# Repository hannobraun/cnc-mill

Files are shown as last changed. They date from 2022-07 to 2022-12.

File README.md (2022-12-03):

# CNC Mill

## Goal

I'd like to have a 3-axis CNC mill. I've considered buying one, but everything I can find violates one or more of the following constraints:

- **Budget:** It's going to be my first CNC mill, so spending a lot of money doesn't make much sense. The main purpose is to learn, and figure out what I actually need in a CNC mill. For that reason, I'd like to keep the budget below 1000€.
- **Capability:** At the same time, I don't want to buy a machine that I will outgrow within the first week. It should be capable of cutting aluminium.
- **Space:** I'm severely limited on space. It needs to comfortably fit on a desk.
- **Environment:** I don't have a proper workshop, unfortunately. The machine will need to run in my apartment, preferably without disturbing the neighbors.

There simply doesn't seem to be a machine like this, which is not a surprise. For this reason, I'd like to try and build my own, purpose-made for my use case.

I suspect it might simply be impossible to fulfill all of these requirements within the limited budget. If that is the case, I'm looking forward to learning what the limitations are specifically. I'm also aware that there's a high risk that a self-built machine will fall short in some or all of these areas. I think it's still likely to be a good investment, for the learning experience alone.

## Status

This project has stalled while in the planning phase. I was at the point where the calculations I wanted to do were way beyond my knowledge, so I had to do quite a bit of studying to make progress. Then my daily schedule shifted from under me and I was left with very little time to continue doing that.

I'm sure at some point, I'll have both the desire and the time to design my own CNC mill again. Whether I'll pick back up here when that time comes, or if I decide to start fresh, I don't know.

## License

This project is open source. All documents, design files, and software in this repository are available under the terms of the [Zero Clause BSD License] (0BSD, for short). This basically means you can do anything with them, without any restrictions, but you can't hold the authors liable for problems.

See [LICENSE.md] for full details.

[Zero Clause BSD License]: https://opensource.org/licenses/0BSD
[LICENSE.md]: LICENSE.md

## Design Decisions

Here are some high-level design decisions I've made. None of them are final, and they might still change as I do more research:

- **Configuration:** Fixed gantry. The advantages are just too big, and I think I can live with a smaller work area in one axis.
- **Size:** 40x40x40 cm³ or thereabouts. Those are outer dimensions. If it turns out that this leaves not enough working area, I can go a bit larger, especially in height.
- **Spindle:** 1.5 kW air-cooled AC spindle. Should be strong enough to do well in aluminium and avoids the additional complexity of water-cooling.
- **Axis motors:** Stepper motors. I haven't really looked into servos, but seeing how many machines run just fine with steppers, I'm pretty confident they will work for me. An open-loop control system will also reduce cost and complexity.

## Parts

- eBay
  - [Zhong Hua Jiang 1.5 kW Air-Cooled CNC Spindle Motor 80mm](https://www.zhonghuajiangspindle.com/1.5kw-cnc-air-cooled-spindle-motor-80mm.html): Those are widely available on eBay. Preferably ER16, but ER11 is acceptable.
  - 1.5 kW Huanjang VFD: there are sets of those and the aforementioned spindle available
- Sorotec
  - [Spindle Clamp](https://www.sorotec.de/shop/Spindelhalter-f-r-80mm-HFS-Spindeln-4085.html): Lots of the spindle/VFD sets on eBay come with a clamp, but those don't have mounting holes. This one looks nicer.

## Research Notes

These are the notes from my research process.

### Other Machines

It's going to make sense to take inspiration from other machines at some point. Here are some links:

- [**OpenBuilds**](https://openbuilds.com/): Lots of machines of all kinds.
- [**MPCNC**](https://docs.v1engineering.com/mpcnc/intro/): Interesting design. Less traditional than what I have in mind.
- [**Tormach xsTECH**](https://tormach.com/machines/routers/xstech-router.html): Really interesting machine, in terms of configuration, form factor, and enclosure. Pretty much what I want to build, but hopefully I can fit some more rigid components into the budget.
- [**PrintNC**](https://wiki.printnc.info/en/home): Moving gantry design with a frame based on steel tubing.
- [**Millennium Mill**](https://www.reddit.com/r/MilleniumMachines/): C-frame mill based on aluminium extrusion.
- [**ULTIMATE Bee**](https://bulkman3d.com/knowledge-base/ultimate-bee/): Classic moving gantry design, with what looks like high-quality components.
- [**PocketNC**](https://pocketnc.com/): 5-axis desktop CNC mill. Interesting, in that it is used for milling aluminium (easy to find examples on YouTube), but has a relatively weak spindle (200W).
- [**Nomad**](https://carbide3d.com/nomad/): Pretty close to what I would like to build, in regards to the configuration, form factor, and enclosure. Notable for its weak spindle (70W).

### Online Shops

I'm looking into two groups of online shops:

- Local (i.e. European) shops, because that gives me a minimum of hassle (shipping, customs).
- Shops on platforms like AliExpress or eBay with low prices, as that might be necessary to meet my budget.

European shops:

- [**cnc-technics:**](https://shop.cnc-technics.de/): Have lots of relevant products, but probably too high-end for my budget.
- [**DOLD Mechatronik**](https://dold-mechatronik.de/): Have a lot of different stuff, including aluminium in various sizes. At least some categories seems to be high-priced, relative to the available budget.
- [**Sorotec**](https://www.sorotec.de/shop/): Large selection of all kinds of stuff required for CNCs.
- [**MISUMI**](https://de.misumi-ec.com/): Large selection of materials, mechanical components, and much more. Lots of options for modifying material and aluminium extrusion parts.
- [**Motedis**](https://www.motedis.com/): Materials and mechanical components.

AliExpress:

- [**Bulk Man 3D**](https://www.aliexpress.com/store/1752067) ([also have a website](https://bulkman3d.com/)): Large selection of lots of things I'm going to need.
- [**Makerbase**](https://www.aliexpress.com/store/1047297): Control boards mostly seem not applicable, but the stepper drivers are very interesting.
- [**Zhong Hua Jiang**](https://de.aliexpress.com/store/214974): They manufacture spindles that they sell there, as well as other useful things.

eBay:

- [**motor-mall**](https://www.ebay.de/str/motormall): Chinese shop, ships from Europe. Has spindles and VFDs.
- Those seems to be essentially the same:
  - [**kuku081**](https://www.ebay.de/str/kuku081)
  - [**kuku281**](https://www.ebay.de/str/kuku218)
  - [**kuku86**](https://www.ebay.de/str/kuku86)
  - [**powave21**](https://www.ebay.de/str/powace21)
  - [**rattmmotor**](https://www.ebay.de/str/rattmmotor)
  - [**rattmmotor88**](https://www.ebay.de/str/rattmmotor88)
  - [**RATTM MOTOR CNC**](https://www.ebay.de/str/rattmmotorcnc)
- [**chinacnczone-de**](https://www.ebay.de/str/cnczonedd)

### Configuration

I believe that the following machine configurations are the strongest contenders:

- **Moving gantry**: Tool moves in all 3 axes.
- **Fixed gantry**: Tool moves in x and z axes, table moves in y axis.

I have ruled out more exotic configurations for my first build (despite having lots of ideas), to reduce overall risk.

References:

- https://cncchronicle.com/fixed_or_moving_gantry_for_cnc_router/<br />
  Compares the two configurations. Has a nice comparison table further down.

### Spindle

I see two potentially viable ways to go, regarding the spindle:

- Cheaper DC spindle, around 500W.
- Mid-range AC spindle, possibly water-cooled.

#### DC Spindles

Advantages of DC spindles:

- There are examples of machines with relatively weak spindles that can definitely mill aluminium, although not fast and with not-so-great surface finish. It might be enough for my needs.
- Cheaper than AC spindles.
- More compact than AC spindles. That doesn't just go for the spindle itself, but also for the hardware needed to control it (a possibly bulky VFD, in the case of AC spindles). Given the size constraints, this is very attractive.
- No dealing with AC power.

Examples of machines with relatively weak DC spindles:

- **PocketNC**: Both the V2-10 and the V2-50 come with a 200W spindle[^1][^2]. And yet it seems capable milling aluminium and more. This video is very interesting: https://youtu.be/7YfRNZbfjaY?t=326
- **Nomad**: Only has a 70W spindle. It's easy to find videos of it milling aluminium, but in the one's I've seen, either the sound is covered by a voiceover, or it sounds horribly chattery. So not a strong case, but interesting none the less.

I think the PocketNC is a strong example here. It's obviously not capable of great speeds, and it starts chattering if the settings are too aggressive. But still, it seems to be capable of producing aluminium parts.

Examples of DC spindles:

- [104W, 10.8k RPM, ER8, ~140€](https://www.ebay.de/itm/384842723224); includes driver and bracket
- [400W, 12k RPM, ER8, ~130€](https://www.ebay.de/itm/255388710895); includes driver and bracket
- [400W, 12k RPM, ER8, ~140€](https://www.ebay.de/itm/384842725572); includes driver and bracket
- [500W, 12k RPM, ER11, ~120€](https://www.ebay.de/itm/403510912800); includes driver and bracket
- [500W, 12k RPM, ER11, ~60€](https://www.ebay.de/itm/174570637963); includes driver and bracket
- [600W, 12k RPM, ER11, ~85€](https://www.ebay.de/itm/384858278032); motor only

[^1]: https://cdn.shopify.com/s/files/1/0077/5477/6623/files/V2-10_Spec_V05.pdf?v=1611173337
[^2]: https://cdn.shopify.com/s/files/1/0077/5477/6623/files/V250CHKCHBSpecSheet.pdf?v=1624559427

#### AC Spindles

Advantages of AC spindles:

- They are simply more powerful. I found information, that 1kW power and 24k max RPM should be good for milling aluminium, and I think everything in that range is an AC spindle.
- Water-cooled AC spindles are pretty common. Those are quieter and more long-lived, and I've been told that water cooling isn't too bad, from a complexity perspective.
- The Chinese ones are still surprisingly affordable, although I have no idea how the quality compares to more expensive ones.

Notes:

- In articles I've read, Huanyang has been called out as a quality brand, and I can find affordable offers with EU-based inventory. Unless the budget turns out to be really tight, or some other information comes to light, I might just go with that.
- Some spindles come in a rectangular form factor, with mounting holes included. Seems more convenient than the round ones.

Examples:

- Air-cooled:
  - [0.8kW, 24k RPM, ER11, ~240€](https://www.ebay.de/itm/174956638303); VFD included
  - [0.8kW, 24k RPM, ER11, ~240€](https://www.ebay.de/itm/185102648864); VFD specified at 1.5kW
  - [2.2kW, 24k RPM, ER20, ~220€](https://www.ebay.de/itm/171841127523); VFD included
  - [2.2kW, 24k RPM, ER20, ~220€](https://www.ebay.de/itm/183100123168); VFD included; not sure, if there's any difference to the previous one
- Water-cooled:
  - [1.5kW, 24k RPM, ER16, ~155€](https://www.ebay.de/itm/185467595787); spindle only
  - [2.2kW, 24k RPM, ER20, ~320€](https://www.ebay.de/itm/185340019340); full set: spindle, VFD, water pump, holder, collets
  - [2.2kW, 24k RPM, ER20, ~350€](https://www.ebay.de/itm/185467757422); VFD included
  - [3.0kW, 24k RPM, ER20, ~165€](https://www.ebay.de/itm/185102654786); spindle only
  - [3.0kW, 24k RPM, ER20, ~285€](https://www.ebay.de/itm/174974637566); VFD included

#### References

- https://mellowpine.com/cnc/how-to-choose-a-cnc-spindle/<br />
  Has very specific recommendations.
- https://mellowpine.com/cnc/best-cnc-spindles/<br />
  Presents some specific spindles and what they're suitable for.
- https://en.wikipedia.org/wiki/Collet#ER_collets<br />
  Just some background info on ER collets, for the mechanically challenged (like me).
- https://www.youtube.com/watch?v=w26DHMccicE<br />
  Upgrades to a 3018. Performance becomes satisfactory with a ~1kW spindle. 500W works, but is really slow.

#### Conclusion

Based on everything I've seen, I've narrowed the spindle selection down to the following criteria:

- 1KW+: Yes, you can mill aluminium with less, but it's far from certain whether the results would be satisfying.
- 24,000 max. RPM: This should be sufficient for my needs, and it seems that within the category of 1kW+, this doesn't further reduce the selection.
- Air-cooled: I can find a few (very few) water-cooled ER16 spindles on eBay, but at this point, I'm happy to accept the reduced complexity. Any difference in noise is probably irrelevant anyway, compared to the milling noise itself.
- AC: I can't find any DC spindles that are powerful enough, so it's not a choice at this point.

Most of the spindles I can find with these parameters are from this manufacturer: [Zhong Hua Jian](https://www.zhonghuajiangspindle.com/)

They have a square spindle that I would prefer: [1.5KW 1500W Air Cooled Spindle Square CNC Spindle Motor ER11/ER16](https://www.zhonghuajiangspindle.com/1.5kw-cnc-square-air-cooled-spindle-motor.html)

Unfortunately that's the one that I can't find a source for around here.

### Cutting Tools

The cutting tools that are expected to be used are important for various design decisions. Since I don't have very specific use cases in mind, my goal here is to get a feel for the range of tooling that I might want to use for aluminium. From there, I'll hopefully have better information to make various design decisions.

Here are some cutting tools that I could find:

- cnc-technics
  - Endmills: https://shop.cnc-technics.de/Fraeser/?view_mode=default&listing_sort=&listing_count=96
- Dold Mechatronik
  - Drills: https://www.dold-mechatronik.de/Werkzeuge-Bohrer
  - Endmills: https://www.dold-mechatronik.de/VHM-Fraeser
- Sorotec: https://www.sorotec.de/shop/Zerspanungswerkzeuge/
  - Sorotec: https://www.sorotec.de/shop/Zerspanungswerkzeuge/sorotec-werkzeuge/
  - Firstattec: https://www.sorotec.de/shop/Zerspanungswerkzeuge/Firstattec/
  - Datron: https://www.sorotec.de/shop/Zerspanungswerkzeuge/datron-cnc-fraeswerkzeuge/
- Datron: https://webshop.datron.de/industrie-fraeswerkzeuge/?p=1
- Misumi: https://de.misumi-ec.com/vona2/fs_machining/

I've decided to focus my analysis on the Sorotec offerings, as they have a broad selection, and also focus on the class of machine I'm trying to build, roughly. I'm only looking at tools that are specifically recommended for aluminium.

Analysis:

- Diameter, cutting (mm): 0.2 - 60
- Diameter, shaft (mm): 3 - 12
- Length, cutting (mm): 2 - 43
- Length, total (mm): 38 - 110

List of tools taken into account:

- Countersinking
  - https://www.sorotec.de/shop/Zerspanungswerkzeuge/sorotec-werkzeuge/Entgrater---Senker/HM-Senker/
- Deburring/Chamfering/Filleting
  - https://www.sorotec.de/shop/Zerspanungswerkzeuge/sorotec-werkzeuge/Entgrater---Senker/Entgratfraeser-Fasenfraeser/
  - https://www.sorotec.de/shop/Zerspanungswerkzeuge/sorotec-werkzeuge/Entgrater---Senker/Viertelkreisfraeser/
- Drilling
  - https://www.sorotec.de/shop/Zerspanungswerkzeuge/sorotec-werkzeuge/1-8-werkzeuge/HM-Bohrer/bohrer3175/
  - https://www.sorotec.de/shop/Zerspanungswerkzeuge/sorotec-werkzeuge/1-8-werkzeuge/HM-Bohrer/bohrer317565/
  - https://www.sorotec.de/shop/Zerspanungswerkzeuge/sorotec-werkzeuge/vhm-spiralbohrer/
- Engraving
  - https://www.sorotec.de/shop/Zerspanungswerkzeuge/sorotec-werkzeuge/Gravurwerkzeuge/Gravierfraeser/
  - https://www.sorotec.de/shop/Zerspanungswerkzeuge/sorotec-werkzeuge/Gravurwerkzeuge/Gravierstichel--Standard-/
  - https://www.sorotec.de/shop/Zerspanungswerkzeuge/sorotec-werkzeuge/Gravurwerkzeuge/Radienstichel/
- Face Milling
  - https://www.sorotec.de/shop/Zerspanungswerkzeuge/sorotec-werkzeuge/planfraeser-985/Planfraeser/
- Finishing
  - https://www.sorotec.de/shop/Zerspanungswerkzeuge/sorotec-werkzeuge/schlichtfraeser/schlichtfraeser-beschichtet/
  - https://www.sorotec.de/shop/Zerspanungswerkzeuge/sorotec-werkzeuge/schlichtfraeser/schlichtfraeser-unbeschichtet/
- Milling
  - https://www.sorotec.de/shop/Zerspanungswerkzeuge/sorotec-werkzeuge/1-8-werkzeuge/3-175----1-8---Fraeser/2-Schneider-ALU/
  - https://www.sorotec.de/shop/Zerspanungswerkzeuge/sorotec-werkzeuge/1-8-werkzeuge/3-175----1-8---Fraeser/Sonderlaengen-360/2-Schneider-361/
  - https://www.sorotec.de/shop/Zerspanungswerkzeuge/sorotec-werkzeuge/1-schneider/Schaftfraeser-ALU-412/
  - https://www.sorotec.de/shop/Zerspanungswerkzeuge/sorotec-werkzeuge/1-schneider/1-Schneider-Sorotec-PROALU/
  - https://www.sorotec.de/shop/Zerspanungswerkzeuge/sorotec-werkzeuge/1-schneider/einschneider-sorotec-alu-beschichtet/
  - https://www.sorotec.de/shop/Zerspanungswerkzeuge/sorotec-werkzeuge/2-schneider/2-schneider-kurz/
  - https://www.sorotec.de/shop/Zerspanungswerkzeuge/sorotec-werkzeuge/2-schneider/2-schneider-alu-eckradius/
  - https://www.sorotec.de/shop/Zerspanungswerkzeuge/sorotec-werkzeuge/2-schneider/Schaftfraeser-ALU/
  - https://www.sorotec.de/shop/Zerspanungswerkzeuge/sorotec-werkzeuge/RADIENFRAeSER/1-Schneider-PRO/
- Tapping
  - https://www.sorotec.de/shop/Zerspanungswerkzeuge/sorotec-werkzeuge/Gewindefraeser/

Additional notes:

- https://www.sorotec.de/webshop/Datenblaetter/fraeser/schnittwerte.pdf
- https://webseite.sorotec.de/download/fraesparameter/schnittwerte_1_8_sv.pdf
- https://www.sorotec.de/webshop/Datenblaetter/fraeser/fraeser_verwendung_schaftfraeser.png
- https://webseite.sorotec.de/download/fraesparameter/schnittwerte_planfraeser.pdf

### Cutting Forces

*The following is based on some research, and my own not-that-great knowledge about mechanics. For all I know, my complete reasoning could be wrong.*

My thinking is that once I've selected a spindle, I can calculate what maximum cutting force can be achieved using that spindle. With that information, I can then decide how to dimension the linear axes and the frame.

Some reference material on how to calculate cutting force:

- [Cutting Forces in Milling](https://www.ame.com/workholding-wisdom-posts/2021/03/01/cutting-forces-in-milling/)
- [Understanding tangential cutting force when milling](https://www.ctemag.com/news/articles/understanding-tangential-cutting-force-when-milling)
- [Lots of useful formula for milling](https://www.sandvik.coromant.com/en-gb/knowledge/machining-formulas-definitions/pages/milling.aspx)

From the aforementioned references, I got the following formula for computing tangential cutting force:

$F_t = \frac{T_s}{R}$

Where:
- $F_t$: tangential cutting force
- $T_S$: spindle torque
- $R$: cutter radius

Which makes a lot of sense. I can hopefully get the maximum torque rating of the spindle from the manufacturer. If not, I'm sure there's a way to calculate torque from spindle power, but I haven't looked into how to do that.

Given the maximum torque, I can put in the radius of the smallest tool I intend to use. It's quite possible that the resulting force will be larger than the small tool can withstand. But I can just put in larger and larger tools until I get a force that will actually work with the tool, thereby figuring out the maximum tangential cutting force that is actually realistic.

Once I have that number, I need two more:

- Maximum expected tool length
- Distance between tip of maximum length tool and spindle holder.

With that, I can calculate the moment that acts on the spindle, which I can then use to figure out how to dimension the linear hardware on the z and x axes.

*At this point I'm realizing that it would be easier to just do the calculations instead of spelling out how I would do them. I can't though, because I haven't selected a spindle yet, so I'll continue writing out my thoughts on this, so I don't forget between now and when I'll actually do the calculations. (When I started writing this, I just expected there would be much more research and much less reasoning.)*

Side note: It's interesting to note that the worst case for max. tangential cutting force is a thin tool, and worst case for max. moment on the spindle is a long tool. It's probably a good idea to plug in multiple tools into the whole calculation, to figure out where the actual worst case is, since the thinnest tool certainly won't be the longest.

Based on the max. tangential cutting force, I can also figure out the maximum moment that acts on the y axis, and dimension the linear hardware for that too.

I assume with all those moments calculated, I can then figure out what the frame would need to look like to not deflect too much under that level of stress. I don't know how that works though.

### Linear Guides

I figure that within the constraints of a home-built machine, linear rails are the best I can practically do in this category. I've decided to focus my research on those, and see where that leaves me budget-wise. I'll revisit later, if necessary.

Information from online shops:

- ARC/HRC: https://www.dold-mechatronik.de/Profilschienenfuehrungen-ARC-HRC
  - data sheet: https://www.dold-mechatronik.de/documents/Datenblaetter/Linearfuehrungen/Datenblatt-Linearfuehrung-ARC-HRC.pdf
  - seal (Dichtung): S or B
    - S: seals better; recommended for dirty environments.
    - B: less friction
  - preload (Vorspannung): VC, V0, V1, V2
    - VC and V0 have play; only available in lower quality classes (H, N)
    - V1 and V2 don't, but have more friction
    - V1 might be a good compromise, is my initial impression
    - HRC has higher tension than ARC, in the equivalent classes
  - precision class (Genauigkeitsklassen): N, H, P, SP, UP
    - recommended for CNC mills: N to P, or H to SP for more precision
  - bearing cage (Kugelkette): should make sure it's included, unless price is prohibitive
  - standard lengths, minimum: 300mm
  - series:
    - ARC-M: compact, narrow
      - I assume I'll have two rails in every axis, so narrow carriages should be fine. I assume broader ones make sense, if you have just one rail.
    - ARC-F: compact, flange
      - broader than M
    - HRC-M: high, narrow
      - more height above the rail
    - HRC-F: high, flange
      - relates to HRC-M as ARC-F relates to ARC-M
  - sub-series: Each of the previously presented series is further divided into more series. The distinction between those is the size of the carriage that fits a given size rail. Larger ones can take more force.
    - ARC-MS (S = small?): rail sizes from 15x15 to 28x27
    - ARC-MN (N = normal?): rail sizes from 15x15 to 53x46
    - ARC-ML (L = large?): rail sizes from 15x15 to 53x46
- BR: https://www.dold-mechatronik.de/Profilschienenfuehrungen-BR-Serie
  - Can't find a data sheet.
  - BR9 and BR12 available.
  - Only BR12 has some dimensions in the shop. Smaller compared to even the smallest ARC/HRC.
  - Sold in sets of one rail + 2 carriages, which is what I need anyway.
  - Probably not interesting to me, given the small size and lack of information compared to ARC/HRC.
- HG:
  - shop links:
    - DOLD Mechatronik
      - https://www.dold-mechatronik.de/HG-Profilschienenfuehrungen
    - HIWIN
      - https://www.sorotec.de/shop/CNC-Mechanik/lineartechnik/Lineartechnik--Hiwin/Fuehrungswagen/Baureihe-HGH-247/
      - https://www.sorotec.de/shop/CNC-Mechanik/lineartechnik/Lineartechnik--Hiwin/Fuehrungswagen/Baureihe-HGW/
      - https://www.sorotec.de/shop/CNC-Mechanik/lineartechnik/Lineartechnik--Hiwin/Fuehrungsschienen/Baureihe-HGH/
    - Sorotec
      - https://www.sorotec.de/shop/CNC-Mechanik/lineartechnik/sorotec-blue-line-936/
  - data sheet: https://www.dold-mechatronik.de/documents/Datenblaetter/Linearfuehrungen/Datasheet_HGH-HGW_de_210720_Dold.pdf
  - DOLD Mechatronik data sheet is much less detailed than ARC/HRC
  - HIWIN has much more detailed information. See below.
  - Size seems comparable to lower range of ARC/HRC, which I think fits my use case.
- LF: https://www.dold-mechatronik.de/Profilschienenfuehrungen-LF-Serie
  - Sizes seem comparable to lower end of ARC/HRC.
  - Barely anything available at DOLD Mechatronik.
  - The available rails are way too long.
  - Not data sheet.
- LSK: https://www.dold-mechatronik.de/Profilschienenfuehrungen-LSK-Serie
  - data sheet: https://www.dold-mechatronik.de/documents/Dold_LSK_Linearfuehrungen.pdf
  - Sizes seem comparable to lower end of ARC/HRC.
  - FL and GL recommended for machine tools.
  - FL seems lower, possible better suited.
  - pretention (Vorspannung): Z2 (hightest) recommended for machine tools
  - more information in there I didn't go through in detail
  - unclear how this is meaningfully different from ARC/HRC
- MGN:
  - shop links:
    - DOLD Mechatronik
      - https://www.dold-mechatronik.de/MGN-Miniatur-Linearfuehrungen-schmal
    - Sorotec
      - https://www.sorotec.de/shop/CNC-Mechanik/lineartechnik/Lineartechnik--Hiwin/Fuehrungswagen/mgn-baureihe/
      - https://www.sorotec.de/shop/CNC-Mechanik/lineartechnik/Lineartechnik--Hiwin/Fuehrungsschienen/baureihe-mgn-r/
  - much smaller; probably more suited to low-force stuff like printers
- MGW: https://www.dold-mechatronik.de/MGW-Miniatur-Linearfuehrungen-breit
  - MGN, but broad
  - probably unnecessary, compared to MGN, since I'm going for two rails per axis
- MR: https://www.dold-mechatronik.de/MR-Miniatur-Linearfuehrungen
  - data sheet: https://www.dold-mechatronik.de/documents/Datenblaetter/Linearfuehrungen/Datenblatt-Miniaturlinearfuehrung-MR.pdf
  - very small, comparable to MGN/MGW
  - nice data sheet, didn't look into it in detail
  - didn't see anything about applications; probably too small for a mill
- MRW: https://www.dold-mechatronik.de/MRW-Miniatur-Linearfuehrungen-breit
  - same data sheet as MR
  - wide version of MR
- MSB: https://www.dold-mechatronik.de/Profilschienen-MSB-Serie-PMI
  - data sheet: https://www.dold-mechatronik.de/documents/Datenblaetter/Linearfuehrungen/MSB-TE-E.pdf
  - data sheet is sparse
  - size comparable with lower end of ARC/HRC
- ST: https://www.dold-mechatronik.de/ST-Miniatur-Kurzhub-Linearfuehrung
  - shares a data sheet with MRW
  - specialized thing for short movements; probably not interesting

Information from HIWIN:

- full catalogue with lots of information:
  - https://www.hiwin.de/medias/GW-11-4-EN-2207-K.PDF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
  - https://www.hiwin.de/medias/GW-11-4-DE-2207-K.PDF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
- configurator: https://www.hiwin.de/configurator/newConfiguration/easyKAT_GW

Conclusions:

- ARC and HG seem like good options, given the size and available documentation.
- Especially the HIWIN documentation is nice. But in the Sorotec store, HIWIN is also twice as expensive as the Sorotec-branded stuff.

I would need, per axis:

- 2 rails
- 4 carriages

So 6 rails and 12 carriages overall.

Open questions:

- What type should I go with?
- Is HIWIN even an option price-wise? Would it be even worth it? Go for something cheaper?
- What size rail?

### Ball Screws

Much like with linear rails, I figure that the best I can practically do on linear actuators are ball screws. I will do my research on that, and might scale back to something cheaper, if it turns out to be necessary.

References:

- Catalogue from HIWIN
  - https://www.hiwin.de/medias/BS-08-10-DE-2206-K.PDF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
  - https://www.hiwin.de/medias/BS-08-10-EN-2206-K.PDF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

Notes:

- HIWIN:
  - types
    - rolled
      - diameter: 8-63mm
      - typical application: transportation
      - accuracy: T5 - T10
      - less friction and quieter than standard threads
      - nuts
        - FSIDIN, FSCDIN: flange
        - RSI, RSIT: no flange; probably wrong for my use case
    - peeled
      - diameter: 16-80mm
      - typical application: transportation + positioning
      - accuracy: T5 + T7
      - nuts
        - DEB-x
          - flange
          - single nut
          - variants with different kinds of wipers
        - DDB-x
          - flange
          - double nut
          - variants with different kinds of wipers
        - ZE, SE
          - no flange
          - probably wrong for my use case
        - SEM
          - safety nut
          - has some redundancy; correct function guaranteed up until certain play
          - pretty sure I don't need this
    - ground
      - diameter: 6-100mm
      - typical application: positioning
      - accuracy: T0 - T5
      - no stock; only available upon request
      - nuts
        - FSC
          - flange
          - single nut
          - cassette recirculation
        - FDC
          - flange
          - double nut
          - cassette recirculation
        - FSI
          - flange
          - single nut
          - internal recirculation
        - FDI
          - flange
          - double nut
          - internal recirculation
        - RSI, RDI
          - no flange
          - probably unsuited
    - other, seemingly more specialized types available
  - preload needs to be balanced
    - too low: lacks rigidity
    - too high: more friction, reduced service life
  - selection: page 12 of the HIWIN catalogue has a step-by-step guide
  - ball recirculation systems
    - external: tube outside of the nut body
    - internal: tube within the nut
    - cassette: internal, but somehow different? don't understand the description
  - wipers
    - NBR (N): "used in almost all applications"
    - NBR-finger (K): more friction, more resistance against dirt and chemicals
    - felt (F), felt-finger (V): different attributes, but unclear on applications
  - precision
    - T0 is best; don't have a feel for the numbers
    - the better the accuracy, the more limited length is; not relevant for my application
    - recommendations for milling
      - x/y axes: T1-T5
      - z axis: T2-T5
    - play/preload
      - rolled and peeled are delivered with play by default
      - types of preload
        - preloaded single nut: ball size
        - lead offset: not suited for high preloads or high leads
        - preloaded double nuts: distance between nuts
      - preload should not exceed
        - 5% of dynamic load rating for single nuts
        - 10% of dynamic load rating for double nuts
      - should only be preloaded when absolutely necessary
    - load rating
      - Cdyn: load at which 90% of ball screws reach life expectancy of 1 million revolutions
      - C0: load which causes permanent deformation of more than 0.0001 ball diameter
    - drive torque: calculation formulas on page 28
  - shaft ends
    - B, E, F: simple transport applications, low axial forces
    - SFA, SLA: more challenging precision applications
      - SLA: supported bearing (S1, S11, S5)
        - for supporting the non-motor end of the ball screw?
      - SFA
        - fixed bearing (S2, S22, S3)
        - for supporting the motor end of the ball screw?
    - WBK: heavy duty
  - housing for flange nuts
    - suitable for DEB-x, DDB-x, FSCDIN

Looks like I need, per axis:
- ball screw
- flanged nut
- supported bearing
- fixed bearing
- flanged nut housing

Other than that, not sure yet, what conclusions to draw from all this.

Open questions:

- What size screw do I go with?
- What accuracy do I need?
- HIWIN is probably too expensive. Do cheaper options require different research?
- What about preload? The HIWIN data sheet makes it sound like preload should be avoided, if at all possible. But isn't the whole point of a ball screw to avoid backlash?

### Frame

Warning: This section is more of a brain dump, and not based on actual research so far. I'm drawing my own conclusions based on things I've seen in the past, and I'm probably missing something.

I'm mainly thinking about two ways of building the frame:

- Aluminium extrusion
- Aluminium plates

Or a combination of the two. Aluminium extrusion has the advantage of being more flexible and easier to use, while plates would require at least somewhat accurate drilling, if not machining.

To make use of the full flexibility and simplicity of aluminium extrusion though, I need angle brackets to connect them. I don't know how well that would fare in regards to stiffness. I've seen people connect profiles by drilling through one, and putting in a screw that screws in the end of the other, but that would require somewhat accurate drilling again, plus cutting the profiles to length precisely.

I'm guessing connecting plates with screws would be plenty stiff, and I could probably buy them already cut to size. This would only leave the problem of drilling and tapping, which might be manageable. An advantage over extrusion might be that they are just denser. Since more weight is largely good in a machine frame, and space is at a premium, that would probably be an advantage.

At this point I'm thinking, I'll probably do a CAD design based on plates and see where that leads. If it seems doable, I might go that way. If not, I might reconsider doing an extrusion-based design.

### Stepper Drivers

Makerbase: https://www.aliexpress.com/store/1047297
  - standard(?) breakout board pinout
    - Makerbase MKS A4988: https://www.aliexpress.com/item/32888457440.html<br />
      2.0A max
    - Makerbase MKS TMC2208: https://www.aliexpress.com/item/32888980385.html<br />
      2.0A max
    - Makerbase MKS TMC2209: https://www.aliexpress.com/item/33043140087.html<br />
      2.5A max
    - Makerbase MKS TMC2225: https://www.aliexpress.com/item/4001149124672.html<br />
      2.0A max
    - Makerbase MKS TMC2226: https://www.aliexpress.com/item/1005002669282600.html<br />
      2.5A max
  - Makerbase MKS TMC2160: https://www.aliexpress.com/item/1005004044381878.html<br />
    4.33A max
  - Makerbase MKS TMC2160-OC: https://www.aliexpress.com/item/4000185818422.html<br />
    4.33A max, extra cooling

### Control Software

On the controller side I have the following priorities:

- Resist the temptation to do any custom software, or otherwise use something exotic. This might be an option in later builds, but I want to keep it simple for the first version.
- Be controllable from a regular PC, without requiring one to run. I don't want to add a screen/keyboard/mouse to the bill of materials, but I also don't want to dedicate a whole computer to control it.

I found the following options:

- [**LinuxCNC**](https://linuxcnc.org/): Runs on the Raspberry Pi:
  http://linuxcnc.org/docs/stable/html/getting-started/getting-linuxcnc.html

  The download page talks about interface cards. Not sure what specifically is required, but I found this list:
  http://wiki.linuxcnc.org/cgi-bin/wiki.pl?LinuxCNC_Supported_Hardware

  I haven't done much research, but the interface cards I saw were quite expensive. Overall, I get the impression that LinuxCNC is not suited for a budget-sensitive build.

- [**Machinekit**](https://www.machinekit.io/): I found it hard to understand whether this is suitable. What I can gather is that it runs on the BeagleBone Black: https://www.machinekit.io/docs/getting-started/machinekit-images-for-bbb/

  No idea what else is required to make it work. The information presented is not very approachable, and I'm not sure how much of it is outdated.

- [**grbl**](https://github.com/gnea/grbl): I've often heard about this being used for the kind of small-scale CNC machine I'm aiming to build. It's confusing though. There are two different repositories, neither actively developed, and lots of forks.

- [**grblHAL**](https://www.grbl.org/): Fork of gbrl, for 32-bit MCUs.

- [**FluidNC**](https://github.com/bdring/FluidNC): Looks promising. Has a list of supported hardware: https://github.com/bdring/FluidNC/wiki/Hardware-that-Runs-FluidNC

Based on my cursory research into this area, I think this might be the wrong approach. It might be better to search for easily available CNC controllers, and figure out which software to use for them from there.

Host-side control software:
- https://github.com/Denvi/Candle
- https://github.com/winder/Universal-G-Code-Sender
- https://github.com/terjeio/ioSender

### Controller Boards

I'm currently operating under the assumption that an open-loop control system using stepper motors will be used, for cost reasons.

There is a huge number of options available. A lot of them are pricy enough to take up the majority of the available budget. For that reason, I'm focusing on lower-priced options.

TinyG control boards, which include steppers drivers, but lack something to control the spindle:

- https://synthetos.myshopify.com/products/tinyg<br />
  Not the cheapest option ($129.99), but open source and well-documented. Includes 4 stepper drivers (2.5 amps).
- https://synthetos.myshopify.com/collections/assembled-electronics/products/gshield-v5<br />
  Cheaper alternative to the TinyG ($49.99), which requires an Arduino to work. I happen to have an Arduino Due lying around, so that might work out well. Includes 3 stepper drivers (2.5 amps).

Both of those boards don't seem to be available in Europe, so the real cost might be significantly higher, with shipping and customs duties.

SainSmart sells the controller boards for their low-cost CNC machines separately:
- https://www.sainsmart.com/collections/genmitsu-cnc-replacement-upgrade-parts/products/genmtisu-grbl-controller-board-for-3018-prover-3018-mx3
- https://www.sainsmart.com/collections/genmitsu-cnc-replacement-upgrade-parts/products/controller-board-for-genmtisu-cnc-router-3018-3018-pro-1810-rpo

They are much cheaper (40-50€) and can control a spindle. One of them is limited to 1.5-2amps for the stepper motors, the other doesn't specify. Since the SainSmart machines are pretty weak, it's doubtful that the controller board supports any motors (axis or spindle) that would be a significant upgrade over them.

Here's another board, linked to grblHAL:
https://www.tindie.com/products/philba/grblhal-bob-unkit-for-teensy-41-t41u5xbb/

Costs around 50€, plus shipping from the US. Requires a Teensy 4.1, which is readily available locally, for under 30€. Doesn't include stepper drivers, but can control a spindler with an external VFD.

References:

- https://www.cnccookbook.com/cnc-controller-software-drivers-boards/
  Overview over some available options.

### Power Supply

As far as I can see, the machine needs the following kinds of power:

- **230V AC**: Since I'm in Europe, this is the input I'm dealing with. It's needed by the VFD for the spindle, the DC power supply, possibly the water pump.
- **3.3V - 5V DC**: This is the typical range for microcontrollers and many other kinds of electronics.
- **Higher-voltage DC**: The stepper motors are going to need DC at a higher voltage than the controller.

So I'm going to need a power supply that turns AC into DC, and possibly something else to step the DC up or down to meet the different requirements. As for the power supply, I've often seen [Meanwell](https://www.meanwell.com/) in various sets and such. Unless there's a good reason not to, I might just stick to that.

### CAD Software

I'd love to use [Fornjot](https://www.fornjot.app/), but it'll be a while before it's ready for a project like this. I hope that I can migrate the project to Fornjot eventually.

Normally, I'd favor open source software, but since migration to Fornjot at a later stage is planned anyway, I don't see that as a priority. I've used OpenSCAD, FreeCAD, SolveSpace, and other open source options in the past, and I'd like to take this opportunity to try something new.

I'm focusing the research on options that are free (or have a free tier) and support Linux:

- [**OnShape**](https://www.onshape.com/): Looks highly professional. Would certainly be an interesting learning experience.
- [**SketchUp**](https://sketchup.com/): Also looks interesting, although the website presents architecture and furniture use cases, versus the mechanical assemblies showcased on the OnShape website. Hard to say how relevant this will be for this project.
- [**TinkerCAD**](https://www.tinkercad.com/): Looks least interesting, judging from the website, as it stresses the beginner/education use case. Doesn't mean that it won't be more than capable enough for this project though.

### Enclosure

The design goal for the whole machine is to have it run in an apartment environment, if at all possible, without creating the kind of noise that would be unacceptable in such an environment. An enclosure is going to be critical to achieve that.

References:

- https://www.youtube.com/watch?v=1zIFWG3X1DU

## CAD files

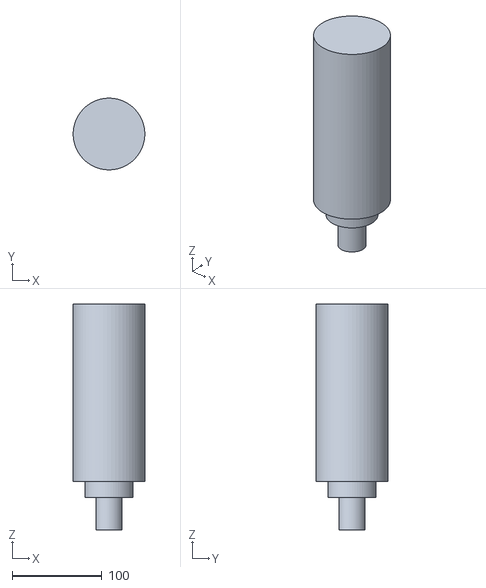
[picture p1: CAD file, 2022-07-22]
cad/Spindle.stl
80.0 x 79.9 x 252.0

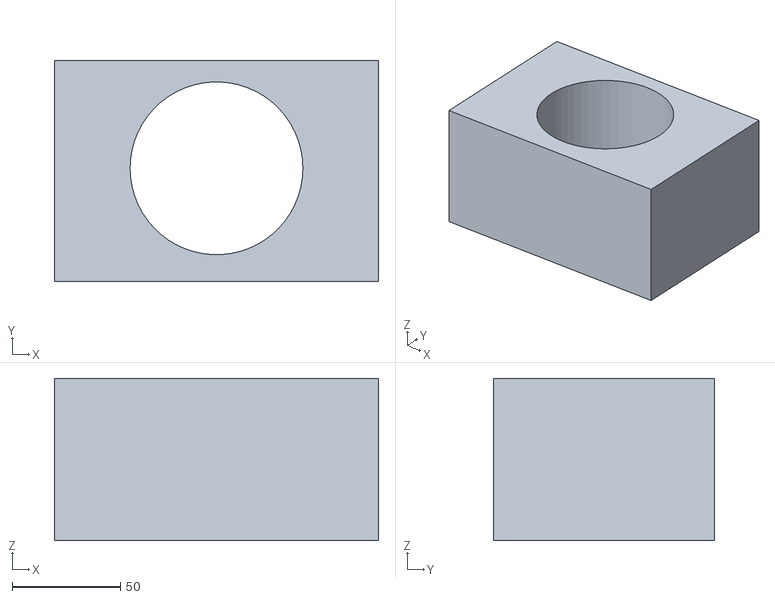
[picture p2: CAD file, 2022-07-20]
cad/Spindle Holder.stl
150.0 x 102.5 x 75.0

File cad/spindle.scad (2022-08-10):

// These are dimensions that are specified in the drawing.
diameter                     =  80;
diameter_collet              =  19;
diameter_neck_base           =  29.5;
diameter_shoulder            =  54;
height_collet                =  13;
height_collet_neck_neck_base =  36;
height_neck_base             =   3;
height_shoulder              =  18;
height_body_bottom           =   8;
height_body_main             = 164;
height_body_top              =  26;
height_total                 = 261;

// These dimensions are derived from the previous ones.
height_neck = height_collet_neck_neck_base
    - height_collet
    - height_neck_base;
height_connector = height_total
    - height_body_top - height_body_main - height_body_bottom
    - height_shoulder
    - height_collet_neck_neck_base;

// These ones are just guesses, as the drawing doesn't say.
diameter_neck      = 15;
diameter_connector = 20;

// Colors
black  = [0.0, 0.0, 0.0, 1.0];
silver = [0.8, 0.8, 0.8, 1.0];

elements = [
    [     height_collet,    diameter_collet,  black], // collet
    [       height_neck,      diameter_neck, silver], // neck
    [  height_neck_base, diameter_neck_base, silver], // neck base
    [   height_shoulder,  diameter_shoulder,  black], // shoulder
    [height_body_bottom,           diameter,  black], // body: bottom
    [  height_body_main,           diameter, silver], // body: main
    [   height_body_top,           diameter,  black], // body: top
    [  height_connector, diameter_connector, silver], // connector
];


// The CNC spindle motor
//
// https://www.zhonghuajiangspindle.com/1.5kw-cnc-air-cooled-spindle-motor-80mm.html
module spindle() {
    union() {
        element(i = 0, elements = elements);
    }

    module element(i, elements) {
        if (i < len(elements)) {
            height   = elements[i][0];
            diameter = elements[i][1];
            color    = elements[i][2];

            color(color)
            cylinder(d = diameter, h = height);

            translate([0, 0, height])
            element(i = i + 1, elements = elements);
        }
    }
}

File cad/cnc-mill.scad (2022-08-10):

use <spindle.scad>;


$fn = 60;


// TASK: What is a good value for the minimum spindle height? I think to answer
//       this question, I think I need to answer the following ones first:
//       1. Do I want to mill to be able to machine its own table?
//       2. If the answer is no:
//          a) What is the thinnest piece of material that I might conceivably
//             machine?
//          a) what is the shortest tool I might conceivably use?
translate([0, 0, 10])
spindle();

table(size_x = 300, size_y = 150, thickness = 10);

module table(size_x, size_y, thickness) {
    translate([0, 0, -thickness / 2])
    cube([size_x, size_y, thickness], center = true);
}

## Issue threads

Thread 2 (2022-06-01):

Makerbase

ahdinosaur, 2022-06-01:
you might be interested: https://makerbase.aliexpress.com/store/1047297

hannobraun, 2022-06-01:
That link is only showing a blank page for me. Maybe it's a temporary error, I'll have a look later. Thanks!

hannobraun, 2022-06-01:
The link still won't work for me, but this one does: https://www.aliexpress.com/store/1047297

Looks like the controller boards are all focused on either 3D printers or servo motors, but they have some really interesting stepper driver boards!

ahdinosaur, 2022-06-02:
yeah as with any direct-from-China supplier it can be difficult to grok the product descriptions, and documentation can often be lacking, but at the same time is usually much bang for buck.

from [the "Hardware that runs FluidNC" page](https://github.com/bdring/FluidNC/wiki/Hardware-that-Runs-FluidNC), seems the Makerbase products that work with FluidNC are:

- [Makerbase MKS DLC32](https://www.aliexpress.com/item/1005003183498253.html) ([GitHub repo](https://github.com/makerbase-mks/MKS-DLC32))
- [Makerbase MKS Tinybee](https://www.aliexpress.com/item/1005003639545394.html) ([GitHub repo](https://github.com/makerbase-mks/MKS-TinyBee))

hannobraun, 2022-06-02:
I swear I looked at all boards in the Makerbase store, but I missed the DLC32. All the others I saw (including the Tinybee) seem to be targeted at 3D printers.

I mean, maybe it doesn't matter in the end, and that "heat bed" output is just some PWM that can be used to control a spindle just as easily. I don't know. Still digging through it all, trying to understand :smile:

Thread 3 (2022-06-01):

BulkMan3D

ahdinosaur, 2022-06-01:
you may be interested: https://bulkman3d.com/ ( https://www.aliexpress.com/store/1752067 )

based on https://openbuilds.com/, i believe is the source of similar maker stores

hannobraun, 2022-06-01:
Thank you! I've only started looking at shops where I can buy parts, so this is very helpful. That link to OpenBuilds is also gold. I was vaguely aware of it, but hadn't thought about it recently.

ahdinosaur, 2022-06-10:
as another example, since you mentioned wanting a gantry-based design, might be worth looking at the latest machine from BulkMan3D, the Ultimate Bee: https://bulkman3d.com/knowledge-base/ultimate-bee/ :bee:

is the latest "OpenBuilds" -style design, but with the latest "best practices" for rigidity: c-beam linear extrusions, linear rails > vslot wheels, ball screws > acme screws.

might be out of your price range though: [bulkman3d.com store](https://bulkman3d.com/product/ultimate-bee-cnc-router-machine-full-kit-ball-screw-quiet-transmission/) | [AliExpress store](https://www.aliexpress.com/store/group/ULTIMATE-Bee-CNC/1752067_40000000306152.html). for me that's mostly because shipping is expensive, maybe [this](https://www.aliexpress.com/item/1005004128570239.html) plus locally sourced components is under budget.

hannobraun, 2022-06-10:
Thanks! More things to look at :smile:

Closed 2022-06-12.

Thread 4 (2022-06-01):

Mostly Printed CNC

ahdinosaur, 2022-06-01:
was looking at [Marlin](https://marlinfw.org/) CNC machines, then stumbled on this: [Mostly Printed CNC](https://docs.v1engineering.com/mpcnc/intro/) :purple_heart:

ahdinosaur, 2022-06-09:
by the way, i found another design with a similar theme: [PrintNC](https://wiki.printnc.info/en/home)

hannobraun, 2022-06-09:
Thanks, that one looks interesting! Much more traditional design than the other one. Will add it to the notes.

Closed 2022-06-09.

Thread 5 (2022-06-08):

OpenBuilds MiniMill?

ahdinosaur, 2022-06-08:
stumbled upon this, might suit your needs? :robot:

https://openbuilds.com/builds/openbuilds-minimill.5087/

available for purchase:

- (expensive) OpenBuilds Part Store: https://openbuildspartstore.com/openbuilds-minimill/
- BulkMan3D:
  - https://www.aliexpress.com/item/32848559381.html
  - https://www.aliexpress.com/item/32865931644.html
- you might find a local supplier (probably supplied by BulkMan3D), e.g. for me [MakerStore.au](https://www.makerstore.com.au/product/osm-mm01/)

hannobraun, 2022-06-08:
Thank you, this does look cool! I'm doubtful that it's for me, for the following reasons:
- I was looking for something with a better work area to total size ratio though (which is why I'm looking into gantry-based designs).
- It's designed to work with a handheld router. I've heard those are very loud (which is a no-go for my use case), and they don't allow for software control of the spindle RPM.
- I see no indication on that page that it can cut aluminium, which I'd like to be capable of.

In addition, I absolutely need an enclosure, but that's not really an argument against this machine. I'll have to build my own with my own design too.

But it's definitely useful to see different designs, and what they are capable of. Seeing machines like this will certainly inform my own design decisions.

I've found this video about the mill, which I don't have time to watch right now: https://www.youtube.com/watch?v=4KVWpFGqT1I

I'll leave this issue open, until I had a chance to watch that video, and maybe look into the design some more.

ahdinosaur, 2022-06-09:
>  I'm doubtful that it's for me, for the following reasons:

fair enough!

by the way, i found a more recent adaptation: "Millenium MiniMill" ([Reddit](https://www.reddit.com/r/MilleniumMachines/) / [Github](https://github.com/MilleniumMills/Millenium-Milo-v1.5)).

> So thanks for nudging me in this direction, @ahdinosaur. Turned into some great learning!

happy to hear these issues are helpful, i hope i'm not being annoying. :purple_heart:

hannobraun, 2022-06-09:
> by the way, i found a more recent adaptation: "Millenium MiniMill" ([Reddit](https://www.reddit.com/r/MilleniumMachines/) / [Github](https://github.com/MilleniumMills/Millenium-Milo-v1.5)).

Nice, I'd seen that before! Of course I wasn't maintaining a research document at the time, so I promptly forgot again.

Seems much sturdier. There are some video of it cutting aluminium: https://www.youtube.com/channel/UCfdxXilZd76Dp8RfLxUJ_Gw/videos

Reopening this issue, until I've added it to my notes.

hannobraun, 2022-06-09:
Oops, forgot to reply to a part of the message.

> happy to hear these issues are helpful, i hope i'm not being annoying. :purple_heart:

You're definitely not annoying! At this point in the process, I'm mostly just looking at stuff, and thinking about how it fits into what I want to build. Just seeing machines, how they're built, what kind of components they use, and where they land budget-wise, is extremely helpful.

Closed 2022-06-09.

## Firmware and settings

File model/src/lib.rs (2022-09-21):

//! Calculations for the CNC mill
//!
//! This is basically a Rust program, in the form of a [Fornjot] model, that
//! does some calculations about the CNC mill, to help to select right-sized
//! components.
//!
//! So, why is this a Fornjot model? Honestly, is doesn't make a whole lot of
//! sense, if viewed in isolation. Fornjot doesn't have the features yet to
//! model the CNC mill's geometry, and it has no simulation features at all. It
//! doesn't really support anything I'm using it for here, and I'd probably be
//! better off just doing it in Excel.
//!
//! However, I want to use Fornjot for modeling the CNC mill (or its successor)
//! in the future, and it makes sense to do this kind of calculation together
//! with the CAD model. I also want Fornjot to at least not stand in the way of
//! use cases outside of its (current) core feature that, and using it for
//! something it wasn't designed for should help there.
//!
//! Lastly, I usually only work on Fornjot itself, within its repository. Using
//! it for something new outside of the repository was already hugely
//! informative, in regards to some weaknesses it has, and where it might trip
//! new users up.
//!
//! [Fornjot]: https://www.fornjot.app/

mod machine;
mod physics;
mod tools;

use std::fmt;

use physics::Power;

use crate::{
    machine::{axes, rails::mgn15_height_total, spindle::Spindle},
    physics::{Force, Radius},
    tools::Tool,
};

#[fj::model]
fn cnc() -> fj::Shape {
    let spindle = Spindle::new(Power::from_value_kw(1.5));
    let tools = Tool::tools();

    let (worst_case_force, tool) = tools
        .into_iter()
        .map(|tool| {
            let (tangential_cutting_force, tool_torque) =
                tool.tangential_cutting_force();

            // Also figure out the torque that would require, and make sure it's
            // below the torque that the spindle can deliver.
            let spindle_torque = spindle.torque(tool.desired_rpm());
            if tool_torque > spindle_torque {
                println!(
                    "Required torque ({tool_torque}) is larger than spindle \
                    torque ({spindle_torque})!",
                );
                println!("Tool: {tool:#?}");
                println!(
                    "Tangential cutting force: {tangential_cutting_force}"
                );

                return (
                    TangentialCuttingForce::PerMaxSpindleTorque(
                        spindle_torque.to_force(tool.diameter),
                    ),
                    tool,
                );
            }

            (
                TangentialCuttingForce::PerToolRequirements(
                    tangential_cutting_force,
                ),
                tool,
            )
        })
        .reduce(|a, b| if a.0 > b.0 { a } else { b })
        .unwrap();

    println!("Worst-case tangential cutting force: {}", worst_case_force);
    println!("Tool: {tool:#?}");

    let y_axis_rail_max_distance_to_force =
        Radius::from_length(axes::y::table_thickness() + axes::z::max_travel())
            + Radius::from_length(mgn15_height_total() / 2.);
    let y_axis_rail_worst_case_torque = worst_case_force
        .value()
        .to_torque(y_axis_rail_max_distance_to_force);
    println!(
        "Worst-case torque at y-axis rail: {}",
        y_axis_rail_worst_case_torque
    );

    // This is a placeholder. We don't actually need to export geometry right
    // now, but Fornjot won't allow us to have a function that doesn't do that.
    let w = 0.5;
    fj::Sketch::from_points(vec![[-w, -w], [w, -w], [w, w], [-w, w]]).into()
}

#[derive(Clone, Copy, Debug)]
pub enum TangentialCuttingForce {
    PerToolRequirements(Force),
    PerMaxSpindleTorque(Force),
}

impl TangentialCuttingForce {
    fn value(self) -> Force {
        match self {
            TangentialCuttingForce::PerToolRequirements(value) => value,
            TangentialCuttingForce::PerMaxSpindleTorque(value) => value,
        }
    }
}

impl PartialEq for TangentialCuttingForce {
    fn eq(&self, other: &Self) -> bool {
        self.value().eq(&other.value())
    }
}

impl PartialOrd for TangentialCuttingForce {
    fn partial_cmp(&self, other: &Self) -> Option<std::cmp::Ordering> {
        self.value().partial_cmp(&other.value())
    }
}

impl fmt::Display for TangentialCuttingForce {
    fn fmt(&self, f: &mut fmt::Formatter) -> fmt::Result {
        write!(f, "{} ", self.value())?;

        match self {
            TangentialCuttingForce::PerToolRequirements(_) => {
                write!(f, "(per tool requirements)")?
            }
            TangentialCuttingForce::PerMaxSpindleTorque(_) => {
                write!(f, "(limited by max spindle torque)")?
            }
        }

        Ok(())
    }
}

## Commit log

2022-05-28 Add research notes on CAD software
2022-05-29 Add research notes on controller boards
2022-06-01 Add research notes on stepper drivers
    Close #2
2022-06-09 Add PrintNC
    Close #4
2022-06-09 Add Millenium Mill
    Close #5
2022-06-16 Add motor-mall
2022-06-16 Add research notes on spindle
2022-06-16 Add info on spindle to design decisions
2022-06-17 Add notes on power supply
2022-06-19 Add more notes on spindle research
2022-06-21 Add notes on enclosure
2022-06-22 Move spindle sections
2022-06-23 Update notes on spindles
2022-06-23 Add examples of AC spindles
2022-06-24 Add examples of DC spindles
2022-06-26 Add notes on linear rails
2022-06-27 Add notes on ARC/HRC linear rails
2022-06-29 Add notes on BR linear rails
2022-06-29 Update HG linear rail links
2022-06-29 Update MGN linear rail links
2022-06-29 Add more notes on linear rails
2022-06-30 Add notes on ball screws
2022-07-03 Revert design decision
    I'm no longer so sure about the spindle. I'll revisit this decision once
    I've had a chance to think on it some more.
2022-07-05 Update notes on ball screws
2022-07-06 Add note on linear rails
2022-07-07 Add notes about frame
2022-07-12 Update notes on spindle
2022-07-19 Add placholder model for spindle
    I've modeled this in OnShape. Experimenting with how that looks in the
    GitHub UI.
    [CNC Mill - Spindle.stl]
2022-07-20 Add spindle holder STL export
    [CNC Mill - Spindle Holder.stl]
2022-07-22 Replace spindle STL
    [CNC Mill - Spindle.stl, Spindle.stl]
2022-07-22 Rename file
    [Spindle Holder.stl]
2022-08-02 Add table
    [cnc-mill.scad]
2022-08-02 Set precision
    [cnc-mill.scad]
2022-08-02 Add first approximation of spindle
    [cnc-mill.scad]
2022-08-02 Move spindle to minimum height
    [cnc-mill.scad]
2022-08-02 Model collet
    [cnc-mill.scad]
2022-08-02 Add documentation
    [cnc-mill.scad]
2022-08-02 Add neck
    [cnc-mill.scad]
2022-08-02 Improve formatting
    [cnc-mill.scad]
2022-08-02 Add neck base
    [cnc-mill.scad]
2022-08-02 Add shoulder
    [cnc-mill.scad]
2022-08-02 Add color to spindle
    [cnc-mill.scad]
2022-08-02 Add bottom part of body
    [cnc-mill.scad]
2022-08-02 Add main part of body
    [cnc-mill.scad]
2022-08-02 Add top of body
    [cnc-mill.scad]
2022-08-02 Fix typo in variable name
    [cnc-mill.scad]
2022-08-02 Add connector
    [cnc-mill.scad]
2022-08-10 Move spindle code to dedicated module
    [cnc-mill.scad, spindle.scad]
2022-08-10 Move variables to top-level
    [spindle.scad]
2022-08-19 Implement function to calculate spindle torque
2022-08-22 Add missing return type
    [lib.rs]
2022-08-24 Add associated constants for min/max spindle RPM
2022-08-25 Limit spindle RPM
2022-08-25 Calculate max torque
2022-09-02 Add `Cut`
2022-09-12 Take max spindle torque into account
2022-09-12 Add `Torque`
2022-09-12 Print tool at max force
2022-09-13 Fix spindle power
2022-09-13 Move `Spindle` to dedicated module
2022-09-21 Calculate worst-case torque at y-axis rail
2022-10-03 Fix case
